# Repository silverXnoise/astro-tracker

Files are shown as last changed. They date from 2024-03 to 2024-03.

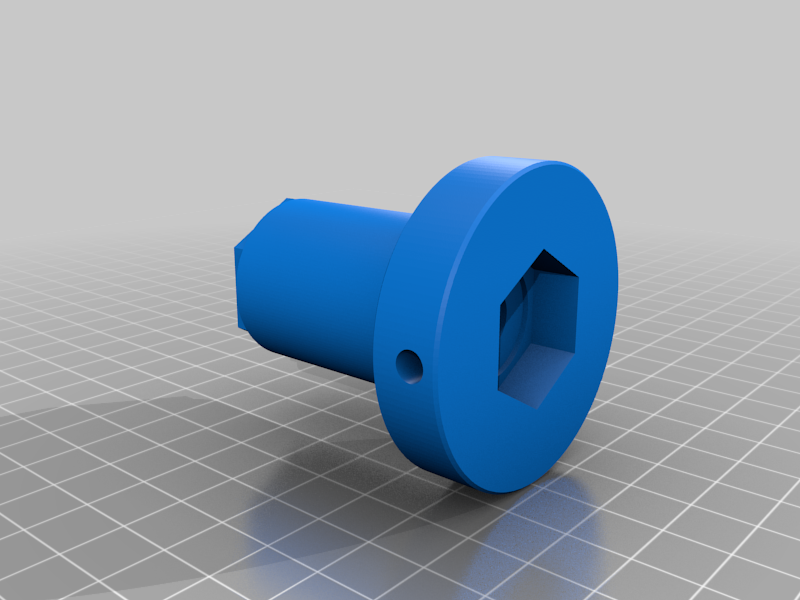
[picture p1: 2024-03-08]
hardware/3D Printed/images/1c67f458-93e8-4dda-88dc-38b02d8965ab.png

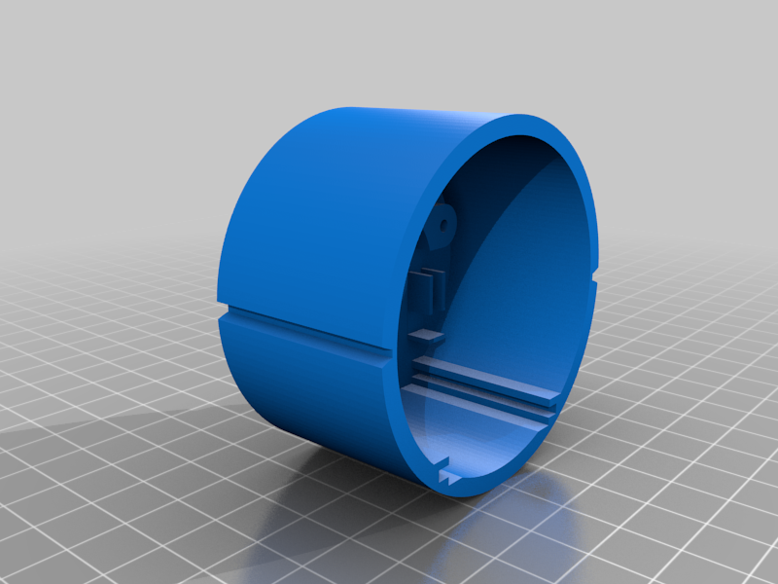
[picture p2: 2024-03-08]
hardware/3D Printed/images/69396c71-a561-4fae-92ba-3e9c0e87c2c8.png

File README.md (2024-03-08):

# HD Astro Tracker

Based on the models and work by [@baokhangnn](https://www.thingiverse.com/baokhangnn) on Thingiverse

## Summary

This is the third generation of the star tracker [@baokhangnn](https://www.thingiverse.com/baokhangnn) started years ago.

This 3D printed star tracker can handle a relatively large lens and camera. Even though the stepper motor is rather small, it leverages gear reduction stages to improve its load capacity. Assuming perfect conditions, the torque output is over 200 ft-lbs!!!

There is a fair bit of backlash, just keep the camera loaded between the 10-11 o'clock position when looking at the output face.

Previous Design: [https://www.thingiverse.com/thing:4879109/](https://www.thingiverse.com/thing:4879109/)

### Print Settings

- Printer brand: Prusa
- Printer: I3 MK3S
- Rafts: No
- Supports: Yes
- Resolution: .2mm
- Infill: 30% Cubic
- Filament brand: Any
- Filament color: Any
- Filament material: PETG
- Notes:
  - Minimum of 3 layers
  - Test print the planetary gears and planetary plate. The gears should spin freely on the plate. If it doesn't, you need to re-calibrate your printer. Possibly adjust your extrusion rate.
  - Once the calibration is satisfactory, print 1X of everything except:  
    - Qty: 5X Part01-Planetary Plate - 5X  
    - Qty: 5X Part13-Sun-Inner - 5X  
    - Qty: 24X Part08-PlanetaryGear - 24X
  - Ring-Body may require support on build plate only.

### Electronics

- 28BYJ-48 w/ ULN2003 Stepper Driver
- Arduino Nano Every
- USB Portable Charger (a 10000mah charger will run this for close to 24 hours!)
- USB cable to power the Nano from the charger.

### Hardware

- 1x 3/8-16 Hex Bolt x 2.5 Long (McMaster# 91268A538)
- 1x 3/8-16 Hex Nut
- 2x 6806-2RS 30mmx42mmx7mm Ball Bearings
- 1x 3mm x 58mm rod or dowel pin
- 1x 1/4-20 Bolt (McMaster# 92949A537)
- 1x 1/4" Washer
- 1x 1/4-20 Coupler (McMaster# 90264A435)
- 2x M3 x 6mm screw (a M3 tap will also be helpful for threading the holes.)

### Optional

- 1-2x Your favorite ball head w/ 3/8-16 mounting.
- 1x Celestron CG-5 PolarScope (#94224)

### MCU Wiring & Programming

Drive the stepper motor at 8.0 rpm. There are plenty of example code for the stepper listed on the internet.

#### Wiring

```plaintext
- Stepper driver: Arduino Uno (Change the pins and code as needed)
- IN1: D4
- IN2: D5
- IN3: D6
- IN4: D7
- Pwr-: GND
- Pwr+: 5V
```

#### Programming

To use the included test code, download and install the `AccelStepper` library into the Arduino programming environment. Then load the TestCode2.ino on to the Arduino. I modded someone else's code to work with my tracker.You can update the code to run at 8RPM as Etaloche pointed out the earth spins a little faster than 24hour to be more accurate!

```cpp
 #include<AccelStepper.h>
 #define HALFSTEP 8
 #define motorPin1 4 // IN1 on the ULN2003 driver 1
 #define motorPin2 5 // IN2 on the ULN2003 driver 1
 #define motorPin3 6 // IN3 on the ULN2003 driver 1
 #define motorPin4 7 // IN4 on the ULN2003 driver 1
 #define switchPin 2 // the number of the pushbutton pin
 #define ledPin 10 // the number of the LED pin

 // initializing AccelStepper
 AccelStepper stepper1(HALFSTEP, motorPin1, motorPin3, motorPin2, motorPin4);

 // variables
 int switchstate = 0; // variable for reading the pushbutton status

 void setup()
 {
  // set AccelStepper-values
  /* Speed: 737.1238124 steps per second in halfstep-mode
   * 4076 Steps per resolution what is the actual resoluton of a 28BYJ-48 Stepper Motor, not the commonly for calculations used 4096
   * 737.1238124 steps per second times 60 seconds makes 44227.428744 steps per minute divided by 4076 steps per resolution makes it 10.850694 RPM for the Stepper)
   */

  /* Speed: 541.853759075 steps per second in halfstep-mode
   * 4076 Steps per resolution what is the actual resoluton of a 28BYJ-48 Stepper Motor, not the commonly for calculations used 4096
   * 737.1238124 steps per second times 60 seconds makes 44227.428744 steps per minute divided by 4076 steps per resolution makes it 10.850694 RPM for the Stepper)
   */

  stepper1.setMaxSpeed(541.853759075);
  stepper1.setAcceleration(50.0);
  stepper1.setSpeed(541.853759075);

  // initialize the LED pin as an output:
  pinMode(ledPin, OUTPUT);

  // initialize the pushbutton pin as an input (switch is connected to GND):
  pinMode(switchPin, INPUT_PULLUP);
  digitalWrite(switchPin, HIGH);
  }
  void loop()
  {
    // read the state of the switch value:
    switchstate = digitalRead(switchPin);
    if (switchstate == LOW) {
        stepper1.runSpeed();
        digitalWrite(ledPin, HIGH);
      }
      else
      {
        stepper1.runSpeed();
        digitalWrite(ledPin, LOW);
      }
  }
```

---

### Post-Printing

#### Head and Gear Train Assembly

1) Assemble the 1/4-20 hex coupler nut into the body. This is where the tripod will mount. Use metal washer and screw through the front opening to secure the coupler.
2) Press Part08 into one of the ball bearings, the install into rear of the the main body. Note orientation is shown in figures. Install front ball bearing.
3) Install nut into face of Part04 and install through front bearing and rear bearing until seated.
4) Assemble hex bolt along with Part05, Part06 (thick or thin depending of bearing choice), and Part09. NOTE: Part09 has a 1 deg taper, the bigger side goes in first. Also press fit the 3mm rod through the hole of Part09. Then insert into rear of housing and screw the bolt through the nut until snug/tight.
5) With a pair of needle nose pliers add the planetary gears to the base planetary plate. There is a small .5mm step on one face of the planets, that should face away from the plate. Again, give it a spin as it should move freely. (see pic)
6) Assemble the Sun-Inner gear into the base planetary plate. And slide down to interface the installed planets. Again, it should be seated and move freely. Then using needle nose pliers add the next set of planets. Repeat this step until all the plates gear and such are in. (see pic)

#### Drive Assembly

1) Assemble stepper motor into Part02 and secure with screws. Then push the Sun\_Drive gear onto the drive shaft of the stepper motor.
2) Connect the Arduino, stepper driver, and stepper motor accordingly. (see wiring below) Then install into Part02. At this point test the electronic to see if it moves. I find it easiest to assemble the drive unit into the housing while it's moving, allows the gears to mesh easily. Should be seated about 1/3 of an inch below the end (see pics).
3) Install back cap and big over lock nut onto the body. The assembly is now complete.

#### Ball Head attachment

1) using a rod / screw drive / Allen key / some pokey thingy insert into the side hole of the mounting plate, then screw on the ball head and tighten. Keep in mind to not load the gear train. Optional: I would attach a second ball head onto the first ball head. This will give you maximum flexibility for setup. Trust me!

#### Polar Scope Assembly

1) Install and screw on the Polar Scope into the alignment port.

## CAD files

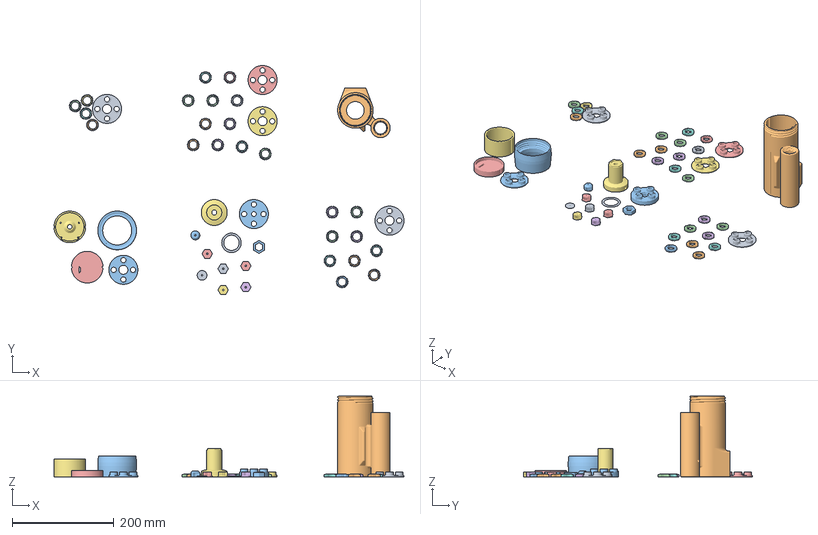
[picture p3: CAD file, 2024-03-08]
hardware/3D Printed/Astro Tracker.3mf
688.0 x 450.1 x 158.8 mm
Part01-PlanetaryPlate_-_5X.STL x 5
Part11-Ring-Body_-_1X.STL
Part05-OutputPlanetaryPlate_-_1X.STL
Part08-PlanetaryGear_-_24X.STL x 24
Part03-LockingCap_-_1X.STL
Part02-DriveHousing_-_1X.STL
Part07-BackCover_-_1X.STL
Part04-MountingPlate_-_1X.STL
Part06-SpacerThick_-_1X.STL
Part10-MountingNutLock_-_1X.STL
Part13-Sun-Inner_-_5X.STL x 5
Part09-AxleGuide_-_1X.STL
Part12-Sun-Drive_-_1X.STL

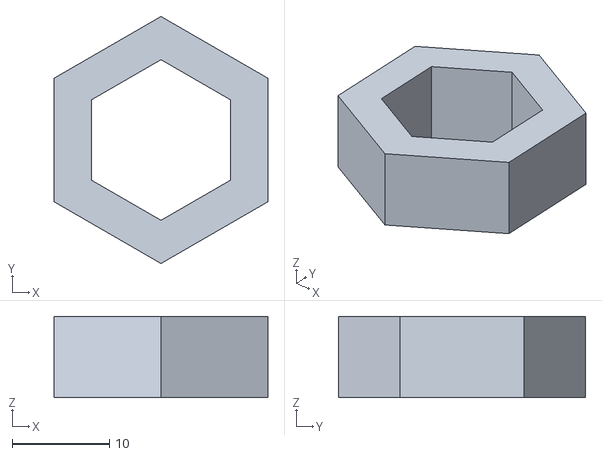
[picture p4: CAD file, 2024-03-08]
hardware/3D Printed/files/Part10-MountingNutLock_-_1X.STL
22.0 x 25.4 x 8.33

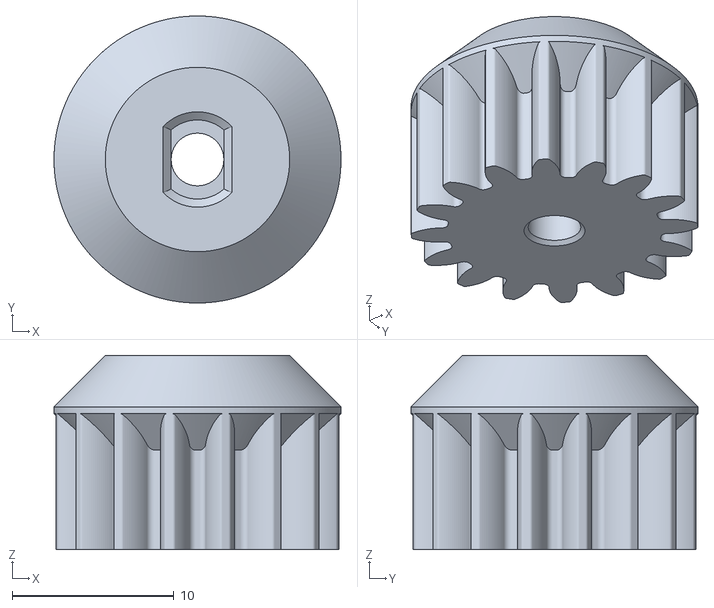
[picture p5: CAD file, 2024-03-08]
hardware/3D Printed/files/Part12-Sun-Drive_-_1X.STL
17.8 x 17.8 x 12.0

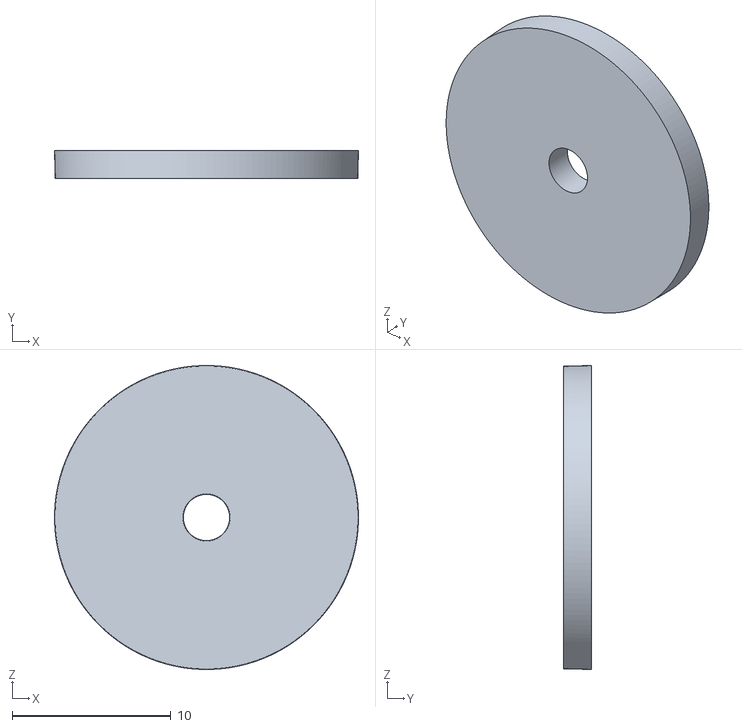
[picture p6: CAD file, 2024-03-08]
hardware/3D Printed/files/Part09-AxleGuide_-_1X.STL
19.1 x 1.78 x 19.1

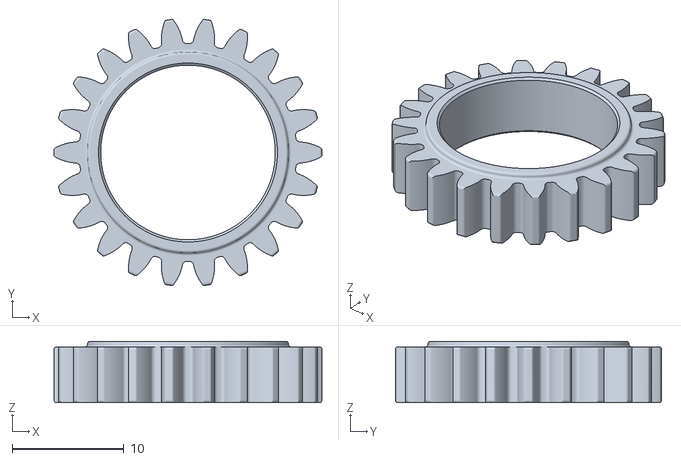
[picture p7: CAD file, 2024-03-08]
hardware/3D Printed/files/Part08-PlanetaryGear_-_24X.STL
24.0 x 23.8 x 5.50

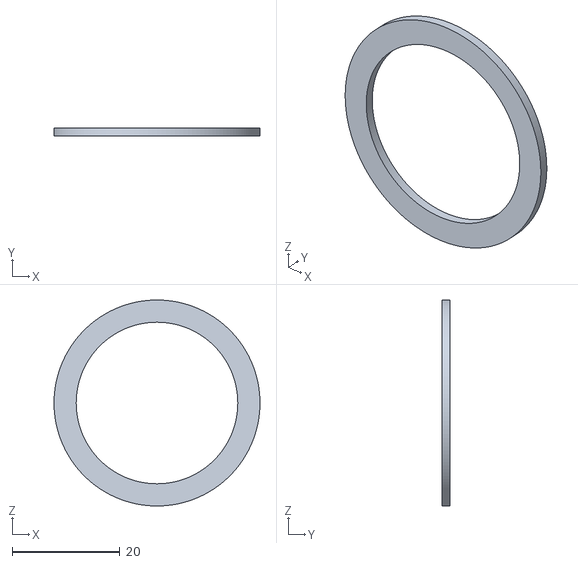
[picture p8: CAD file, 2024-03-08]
hardware/3D Printed/files/Part06-SpacerThick_-_1X.STL
38.3 x 1.50 x 38.3

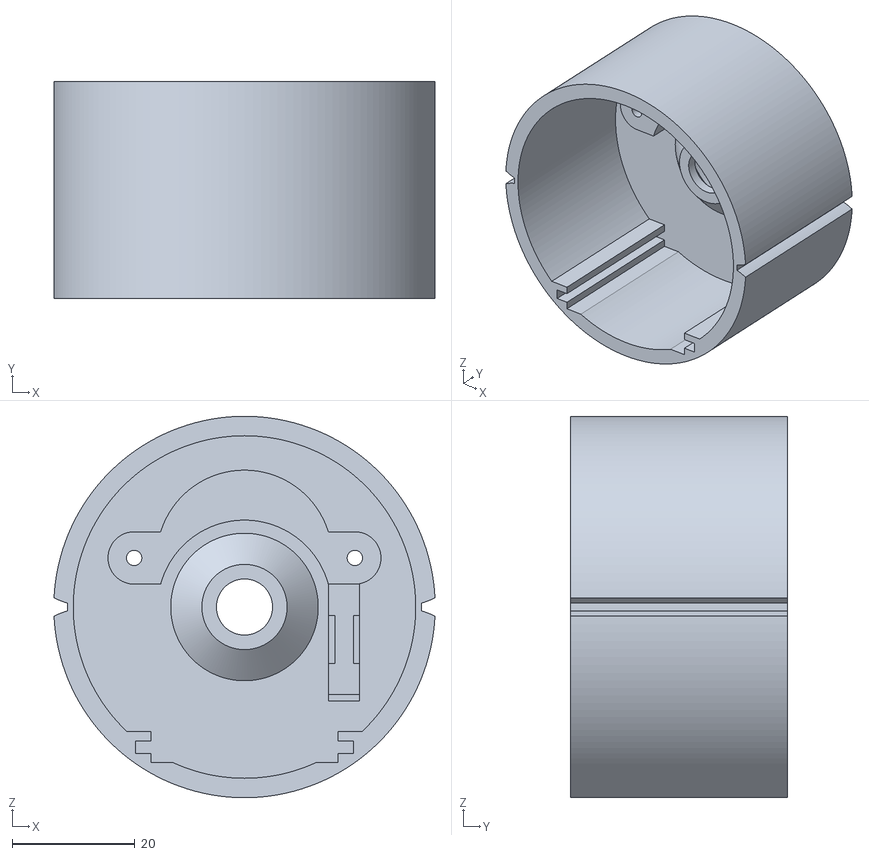
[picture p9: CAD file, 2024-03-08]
hardware/3D Printed/files/Part02-DriveHousing_-_1X.STL
62.2 x 35.4 x 62.2

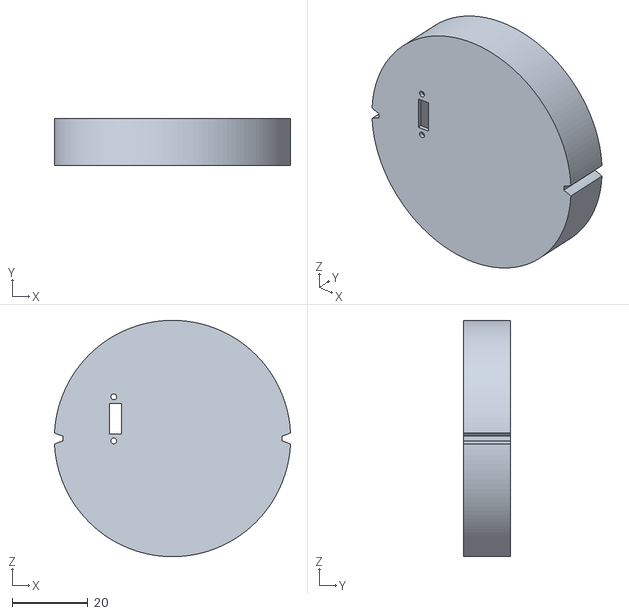
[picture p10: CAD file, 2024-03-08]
hardware/3D Printed/files/Part07-BackCover_-_1X.STL
62.2 x 12.4 x 62.2

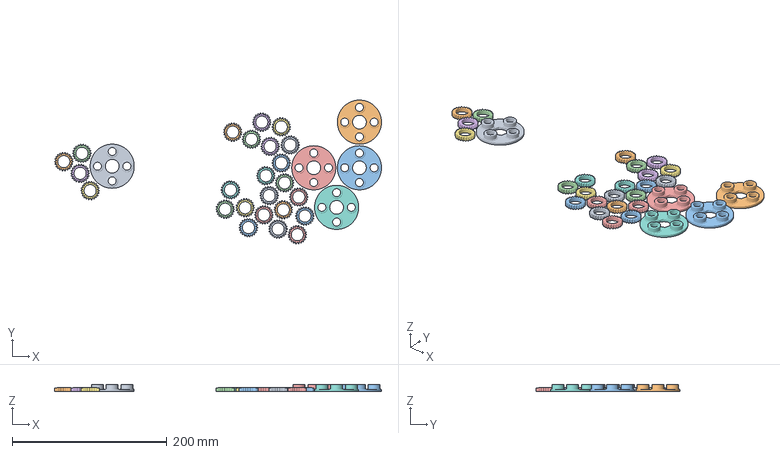
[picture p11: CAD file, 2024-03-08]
hardware/3D Printed/files/Part01-PlanetaryPlate_-_5X.3mf
422.5 x 185.9 x 9.50 mm
Part01-PlanetaryPlate_-_5X.STL x 5
Part08-PlanetaryGear_-_24X.STL x 24

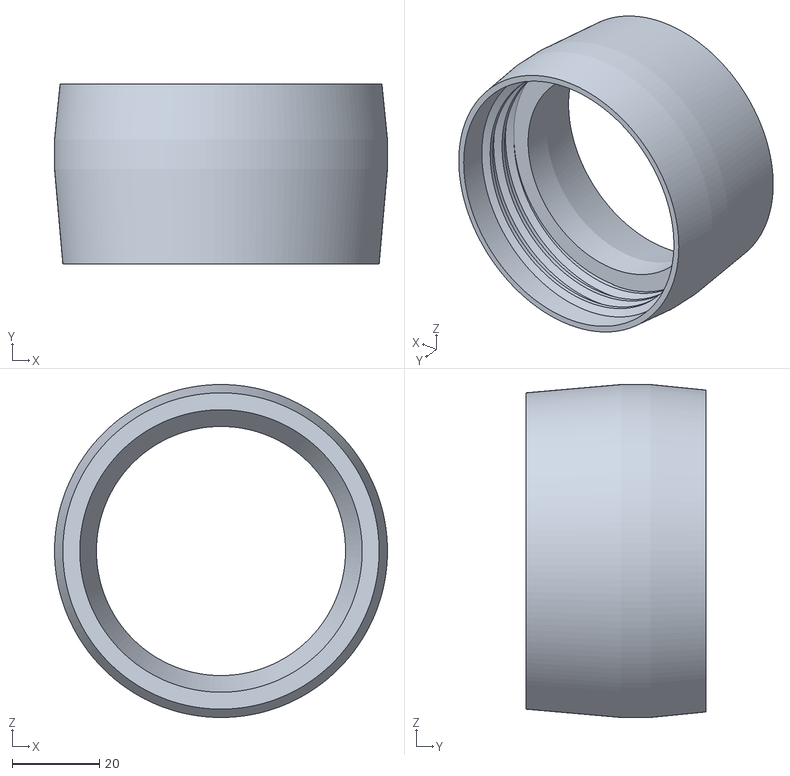
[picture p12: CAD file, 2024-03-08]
hardware/3D Printed/files/Part03-LockingCap_-_1X.STL
76.2 x 41.3 x 76.2

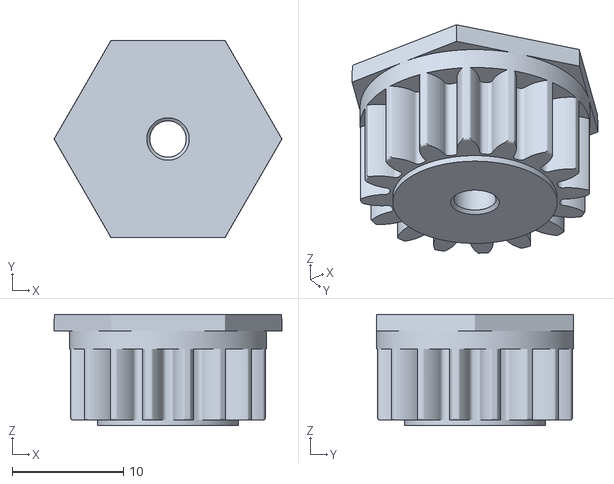
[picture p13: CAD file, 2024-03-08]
hardware/3D Printed/files/Part13-Sun-Inner_-_5X.STL
20.5 x 17.8 x 10.0

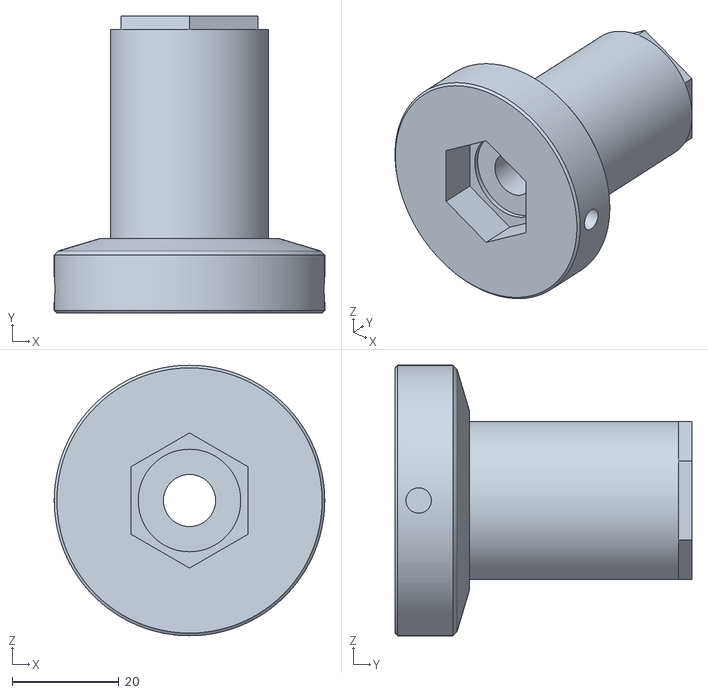
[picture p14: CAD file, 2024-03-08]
hardware/3D Printed/files/Part04-MountingPlate_-_1X.STL
50.8 x 55.8 x 50.8

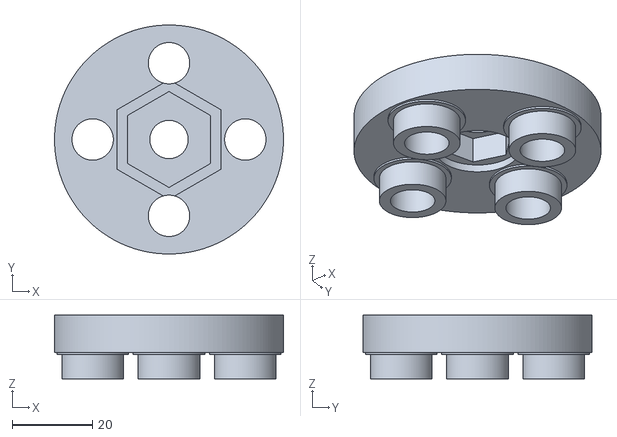
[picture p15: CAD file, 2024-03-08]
hardware/3D Printed/files/Part05-OutputPlanetaryPlate_-_1X.STL
57.0 x 57.0 x 15.9

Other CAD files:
hardware/3D Printed/files/Part01-PlanetaryPlate_-_5X.STL

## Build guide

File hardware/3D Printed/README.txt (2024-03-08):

Gen 3 HD Astro Tracker by baokhangnn on Thingiverse: https://www.thingiverse.com/thing:5847800

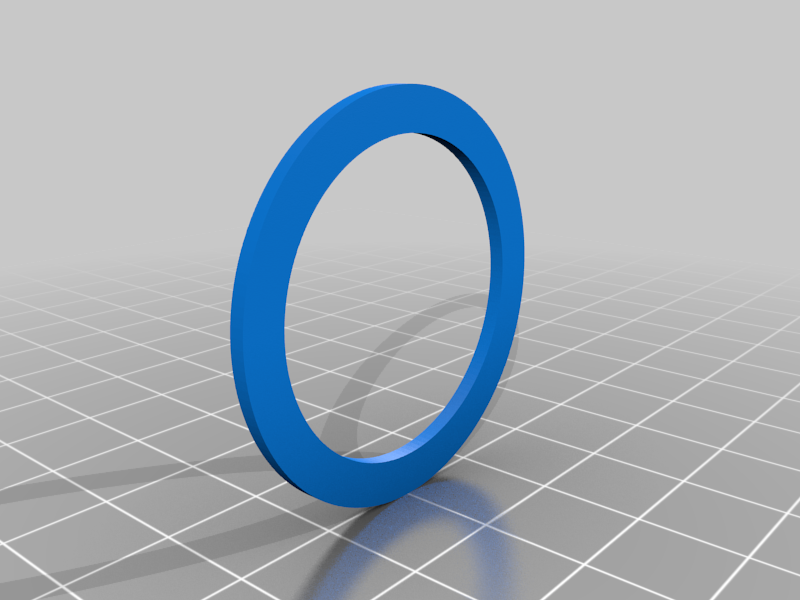
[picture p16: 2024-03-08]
hardware/3D Printed/images/34c72eb5-c0bd-49a4-a1de-ed8d9a0c0e88.png

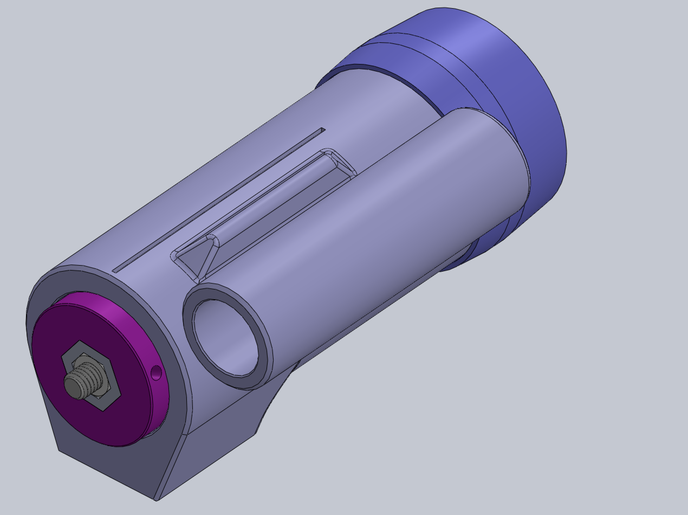
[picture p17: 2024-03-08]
hardware/3D Printed/images/46fe96ae-bd08-4cfe-9264-7e51b2e593e2.png

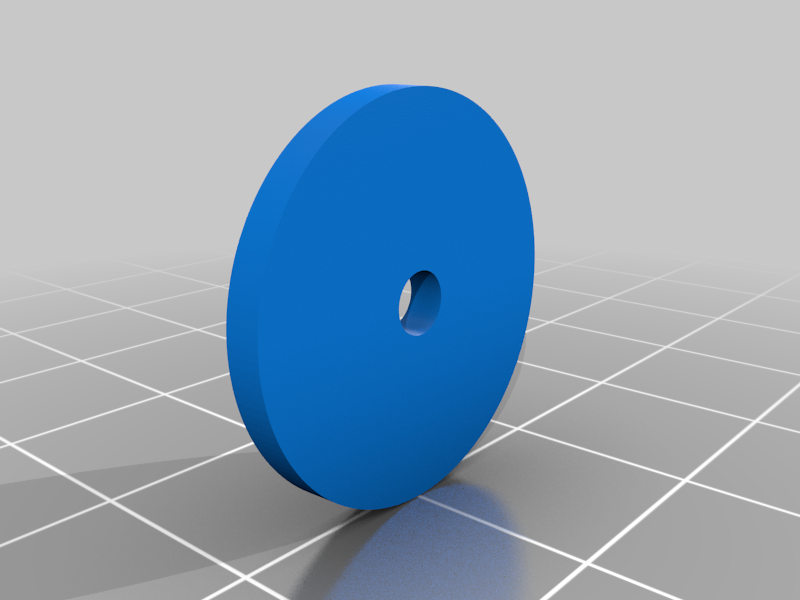
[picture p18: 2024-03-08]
hardware/3D Printed/images/e2a905d9-2b88-4d5f-9047-c91ec733d161.png

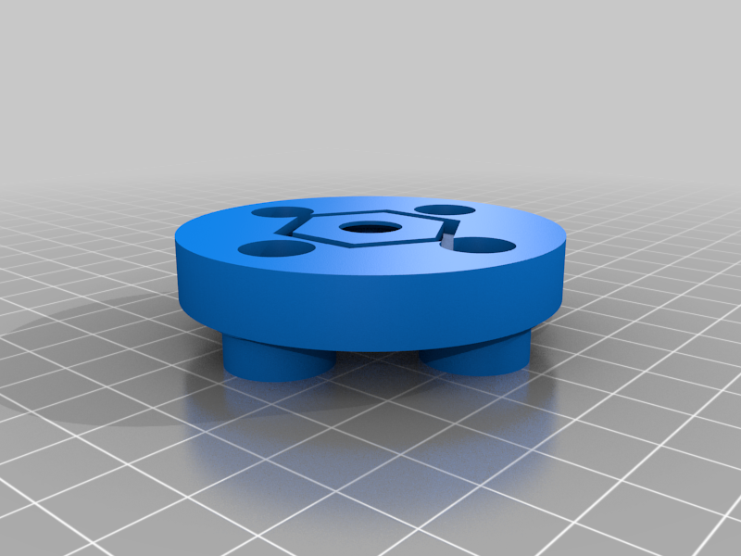
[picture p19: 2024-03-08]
hardware/3D Printed/images/de626251-f7f4-46de-b675-8ca95252a3a2.png
